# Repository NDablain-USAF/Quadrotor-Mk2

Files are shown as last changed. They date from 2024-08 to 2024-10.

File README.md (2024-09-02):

This serves as a repository for the second iteration of the autonmous quadrotor from: https://github.com/NDablain-USAF/Quadrotor
<br /> 
<br /> 
Currently in test and development
<br /> 
<br /> 
Table of Contents:<br /> 
1.0    Table of Changes<br /> 
2.0    Detailed Description of Changes         
<br /> 
<br /> 
<br /> 
1.0 Table of Changes
<br /> 
<br /> 
| Component | Was | Is |
|---:|---|---|
| Frame | Pine Wood | 3D Printed ABS |
| Motor Speed Measurement | Motor Shaft Encoders | Back EMF & ADC |
| Motor Speed Control Hardware | NPN BJT | N-Channel MOSFET |
| Motor Speed Control Software | Lead/Lag Compensator| Proportional/Integral Controller |
| Electrical Connections | Wires,Solder,Perf-Board | PCB |
| Code | C++ | C |
| MCU | Arduino Uno R3 Board | ATMega328P |
| IDE | Arduino | Microchip Studio |
| Attitude Measurement Hardware - Accelerometer | MPU 9250 Breakout Board | BMI 088 |
| Attitude Measurement Hardware - Gyroscope | MPU 9250 Breakout Board | BMI 088 |
| Attitude Measurement Hardware - Magnetometer | MPU 9250 Breakout Board | BMM 350 |
| Attitude Measurement Software | Float operations using Math.h trig. functions | Integers with polynomial trig function approximations |
| Attitude Representation | Euler Angles | Quaternions |
<br /> 
<br /> 
<br /> 
2.0 Detailed Description of Changes
<br /> 
<br /> 
  Frame: Pine wood was initially selected due to its low density, perceived ease of manipulation, and low cost. However, it was found in the Mk1 that the weight of the wood drove higher motor speed and propeller thrust requirements and it was difficult to produce multiple parts to similar dimensions by hand. The higher upfront cost of purchasing a 3D printer will allow for faster part production and replacement rates in the long term along with greater reliability in part tolerances.
  <br /> 
  <br /> 
  Motor Speed Measurement: Removing the requirement of having an integrated shaft encoder opens up a much broader range of motors to choose from, including lower priced ones. Moving from encoder counts triggered by an ISR to sampling the on board ADC allows improved control of measurement sample rate. On the ATMega328P the ADC conversion can be selected at a frequency desired by the designer, and implemented with a timer. An ISR indicates the conversion is complete, and triggers a flag for a measurement function. This greatly reduces the number of interrupts per measurement from potentially hundreds with the encoder to one with the ADC. Additionally the numbers of wires leaving the motor is reduced from five to three. 
  <br /> 
  <br /> 
  Motor Speed Control Hardware: Bipolar Junction Transistors (BJTs) require current through their base to drive current through their collector-emitter junction. This allows for a faster switching time as well as amplification as opposed to just binary saturation but requires additional components as in most cases the current supplied by an MCU IO pin is not enough to fully open the collector-emitter junction. On the other hand, a Metal Oxide Semiconductor Field Effect Transistor (MOSFET) only requires a voltage potential differenc on its gate, no current is required. This change will reduce the number of components required to control the motor speeds, decreasing cost and complexity.
  <br />
  <br />
   Motor Speed Control Software: The initial quadrotor used a lead/lag compensator to control motor speeds. This provided excellent performance, but had a higher computational complexity. First off, there were five terms to tune between the lead compensator gain, and the two poles and zeros. 4 integrals had to be taken and kept track of per motor resulting in a high RAM useage. Switching to a Proportional-Integral controller will reduce the instantaneous computation as well as the number of variables stored in RAM as only one integral will need to be maintained per motor.
   <br />
   <br />
   Electrical Connections: Hand-made connections were the primary method of attaching devices on the initial quadrotor. This allowed for rapid prototyping and the ability to easily swap damaged parts, but also drastically increased production time and quality errors. Most electrical components will be contained on a centralized PCB, several components such as the LoRa module and PA1616S GPS module will be kept on breakout boards and attached via headers to the main PCB. Hand-made connections to the motors will still have to be made with decoupling capacitors directly soldered across the motor terminals.
   <br />
   <br />
   Code: The decisions to switch from C++ to C is mainly based on the desire to learn more about the C language and perhaps reduce some of the technical baggage that can come with using C++. This means the code will take a functional approach rather than object oriented one. This will mean not using the Arduino.h libraries and instead programming primarily off of the MCU data sheet using direct register manipulation. This will allow for direct control over peripherals such as timers,counters,interrupts, and the analog to digital converter. This will likely increase development time but allow for a depper understanding of the working of the MCU.
   <br />
   <br />
Controller PCB: Screenshot (123)
  <br />
Drone PCB: Screenshot (124)
  <br />
Drone Assembly: Screenshot (125)
  <br />

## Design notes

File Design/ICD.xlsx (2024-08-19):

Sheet: CONOPS
MCU 1 will control the inner two loops to include motor speeds and attitude. It will sample the IMU and Magnetometer and be responsible for interpretting the incoming information to determine its own attitude and generate a control signal. It will generate its own motor speed references. It will receive as input a desired orientation and desired thrust, it will compensate the thrust with feedforward control based off its attitude information.

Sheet: Interface List
Component | Connects To | Via | Notes
MCU 1 | MCU 2 | SCL/PC5 | Directly
MCU 1 | MCU 2 | SDA/PC4 | Directly
MCU 1 | MCU 2 | PCINT23/PD7 | Start | PC6 | 1 | MCU 1 | 28 | PC5
MCU 1 | MCU 2 | RST/PC6 |  | PD0 | 2 |  | 27 | PC4
MCU 1 | BMM 350 | SCL/PC5 | Via logic level converter | PD1 | 3 |  | 26 | PC3
MCU 1 | BMM 350 | SDA/PC4 | Via logic level converter | PD2 | 4 |  | 25 | PC2
MCU 1 | BMM 350 | PCINT0/PB0 | Interrupt | PD3 | 5 |  | 24 | PC1
MCU 1 | BMI 088 | SCL/PC5 | Via logic level converter | PD4 | 6 |  | 23 | PC0
MCU 1 | BMI 088 | SDA/PC4 | Via logic level converter | VCC | 7 |  | 22 | GND
MCU 1 | BMI 088 | PCINT18/PD2 | Interrupt (Accel) | GND | 8 |  | 21 | AREF
MCU 1 | BMI 088 | PCINT20/PD4 | Interrupt (Gyro) | PB6 | 9 |  | 20 | AVCC
MCU 1 | Transistor 1 | OC0A/PD6 | Save 16 bit timer (Timer1) for internal timing of interrupts | PB7 | 10 |  | 19 | PB5
MCU 1 | Transistor 2 | OC0B/PD5 |  | PD5 | 11 |  | 18 | PB4
MCU 1 | Transistor 3 | OC2A/PB3 |  | PD6 | 12 |  | 17 | PB3
MCU 1 | Transistor 4 | OC2B/PD3 |  | PD7 | 13 |  | 16 | PB2
MCU 1 | Voltage Divider 1 | ADC0/PC0 | ADMUX register must be changed with right input channel prior to read, but not during a read, perhaps cycled during interrupt | PB0 | 14 |  | 15 | PB1
MCU 1 | Voltage Divider 2 | ADC1/PC1
MCU 1 | Voltage Divider 3 | ADC2/PC2
MCU 1 | Voltage Divider 4 | ADC3/PC3
MCU 1 | Header 1 | VCC | Group Header pins for easy connection to ISP
MCU 1 | Header 2 | GND
MCU 1 | Header 3 | SCK/PB5
MCU 1 | Header 4 | MISO/PB4
MCU 1 | Header 5 | MOSI/PB3
MCU 1 | Header 6 | RST/PC6
MCU 1 | Header 7 | SS/PB2
MCU 1 | Crystal Oscillator | XTAL1/PB6 | Share oscillator with MCU 2
MCU 1 | Crystal Oscillator | XTAL2/PB7
MCU 1 | Logic Level converter | OE/PB1
 |  |  |  | PC6 | 1 | MCU 2 | 28 | PC5
MCU 2 | MCU 1 | SCL/PC5 | Directly | PD0 | 2 |  | 27 | PC4
MCU 2 | MCU 1 | SDA/PC4 | Directly | PD1 | 3 |  | 26 | PC3
MCU 2 | MCU 1 | PD4 | Start | PD2 | 4 |  | 25 | PC2
MCU 2 | MCU 1 | PD7 | Reset | PD3 | 5 |  | 24 | PC1
MCU 2 | Header 1 | VCC | Group Header pins for easy connection to ISP | PD4 | 6 |  | 23 | PC0
MCU 2 | Header 2 | GND |  | VCC | 7 |  | 22 | GND
MCU 2 | Header 8 | SCK/PB5 |  | GND | 8 |  | 21 | AREF
MCU 2 | Header 9 | MISO/PB4 |  | PB6 | 9 |  | 20 | AVCC
MCU 2 | Header 10 | MOSI/PB3 |  | PB7 | 10 |  | 19 | PB5
MCU 2 | Header 11 | RST/PC6 |  | PD5 | 11 |  | 18 | PB4
MCU 2 | Header 12 | SS/PB2 |  | PD6 | 12 |  | 17 | PB3
MCU 2 | Crystal Oscillator | XTAL1/PB6 | Share oscillator with MCU 1 | PD7 | 13 |  | 16 | PB2
MCU 2 | Crystal Oscillator | XTAL2/PB7 |  | PB0 | 14 |  | 15 | PB1
MCU 2 | BMP 390 | SCK/PB5 | Via logic level converter
MCU 2 | BMP 390 | MISO/PB4 | Via logic level converter
MCU 2 | BMP 390 | MOSI/PB3 | Via logic level converter
MCU 2 | BMP 390 | CS/PB1 | Via logic level converter
MCU 2 | BMP 390 | PCINT18/PD2 | Interrupt, via logic level converter
MCU 2 | PA1616S | RXD/PD0
MCU 2 | PA1616S | TXD/PD1
MCU 2 | LoRa | SCK/PB5
MCU 2 | LoRa | MISO/PB4
MCU 2 | LoRa | MOSI/PB3
MCU 2 | LoRa | CS/PD6
MCU 2 | LoRa | GO/PB0
MCU 2 | LoRa | RST/PD5
MCU 2 | Voltage Divider | ADC0/PC0 | Track battery voltage level

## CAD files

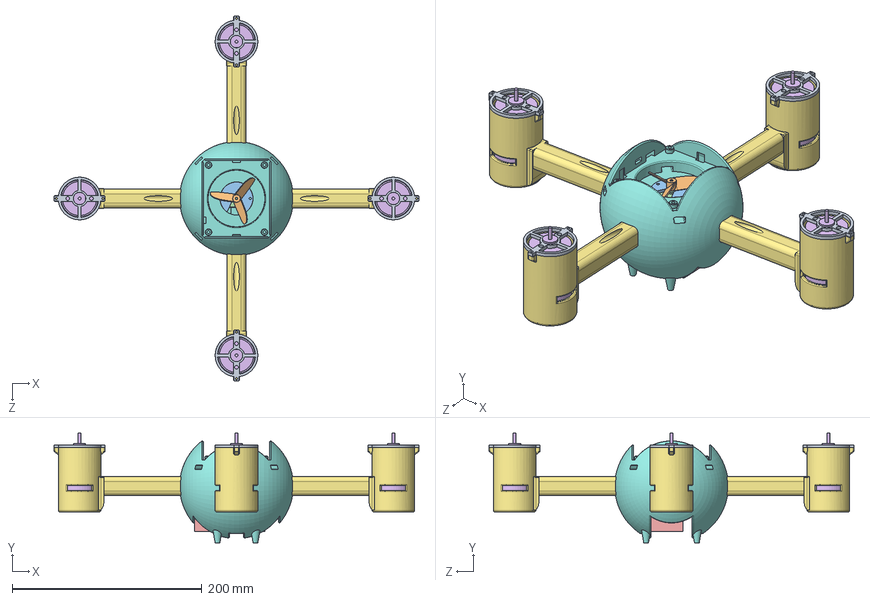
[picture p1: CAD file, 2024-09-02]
Design/Mechanical/Drone_Mark_2_v2.SLDASM
385.0 x 116.0 x 385.0 mm
Body_v2
Motor_Holder_v2 x 4
Motor x 4
Battery_3S_1500
Motor_2
Motor_2_Cover
Fan
Motor_Cover x 4

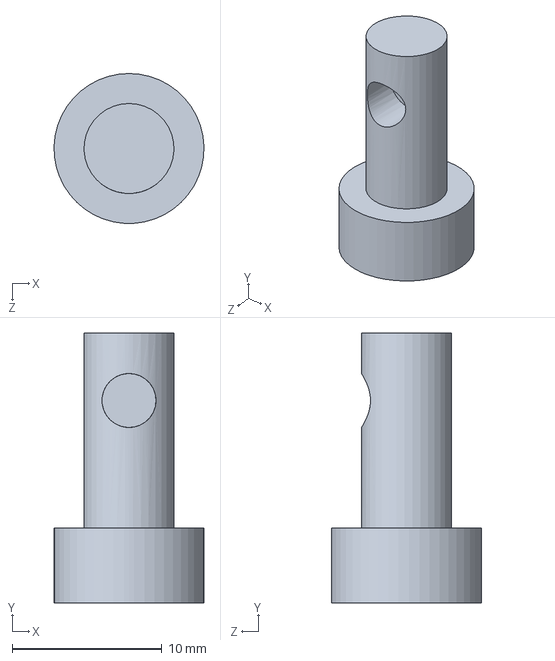
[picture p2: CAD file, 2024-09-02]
Design/Mechanical/Shaft_Extender_2.SLDPRT
9.99 x 18.0 x 10.0 mm

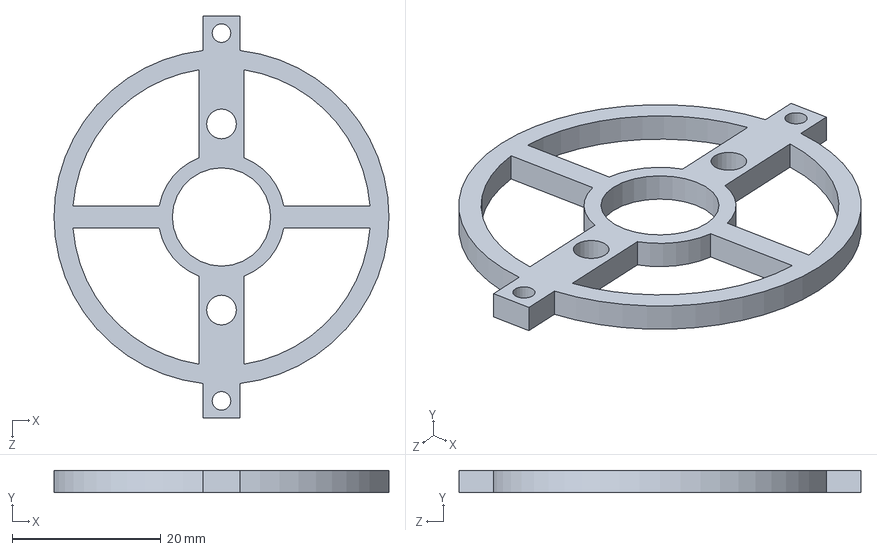
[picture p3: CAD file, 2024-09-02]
Design/Mechanical/Motor_Cover.SLDPRT
45.0 x 3.00 x 54.0 mm

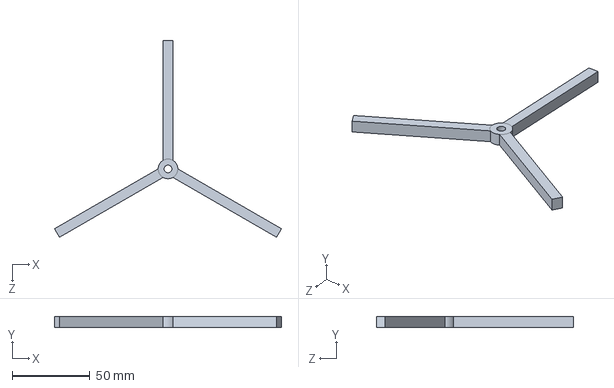
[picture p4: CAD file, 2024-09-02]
Design/Mechanical/BD6x4.2E-3-B4.SLDPRT
146.2 x 6.86 x 126.6 mm

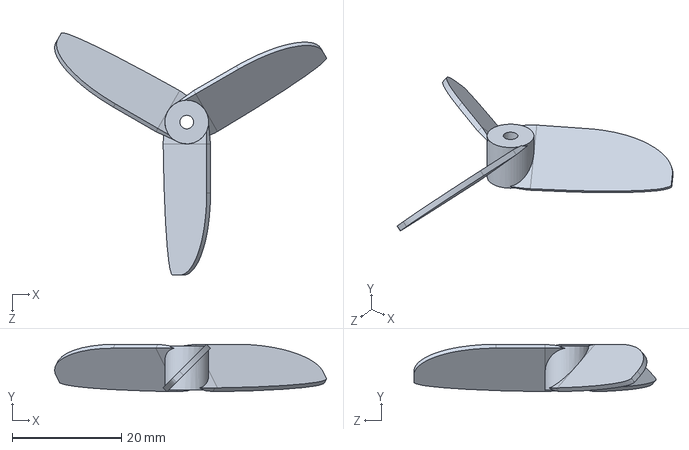
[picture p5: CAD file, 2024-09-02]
Design/Mechanical/Fan.SLDPRT
49.7 x 8.67 x 44.3 mm

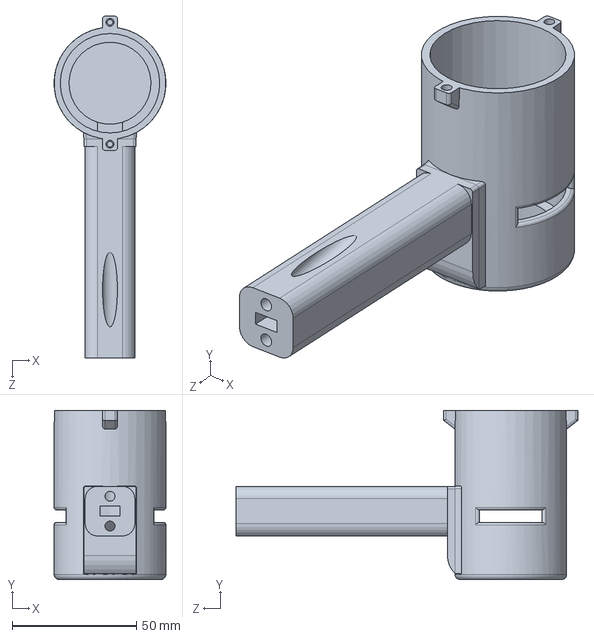
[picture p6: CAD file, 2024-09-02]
Design/Mechanical/Motor_Holder_v2.SLDPRT
45.0 x 68.0 x 137.5 mm

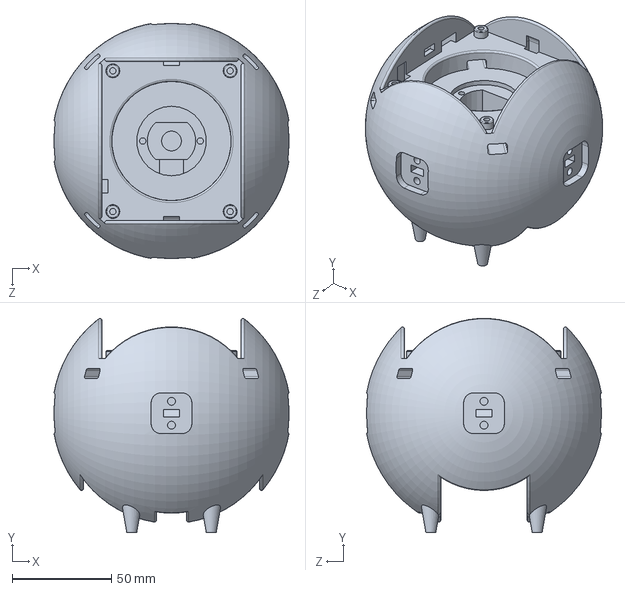
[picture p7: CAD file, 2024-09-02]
Design/Mechanical/Body_v2.SLDPRT
118.2 x 107.7 x 118.2 mm

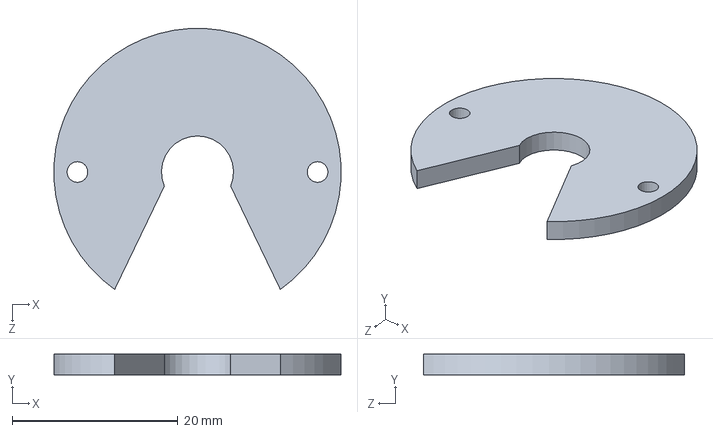
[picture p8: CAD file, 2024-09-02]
Design/Mechanical/Motor_2_Cover.SLDPRT
34.6 x 2.50 x 31.5 mm

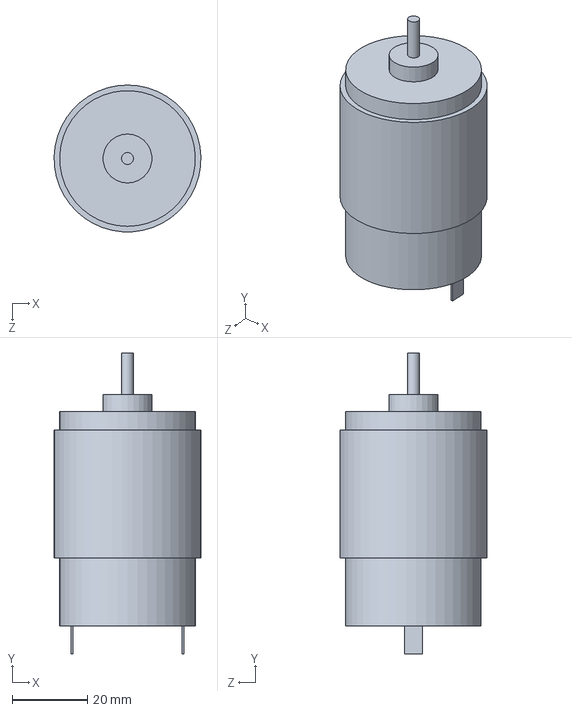
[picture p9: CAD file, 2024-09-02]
Design/Mechanical/Motor.SLDPRT
39.0 x 79.9 x 39.0 mm

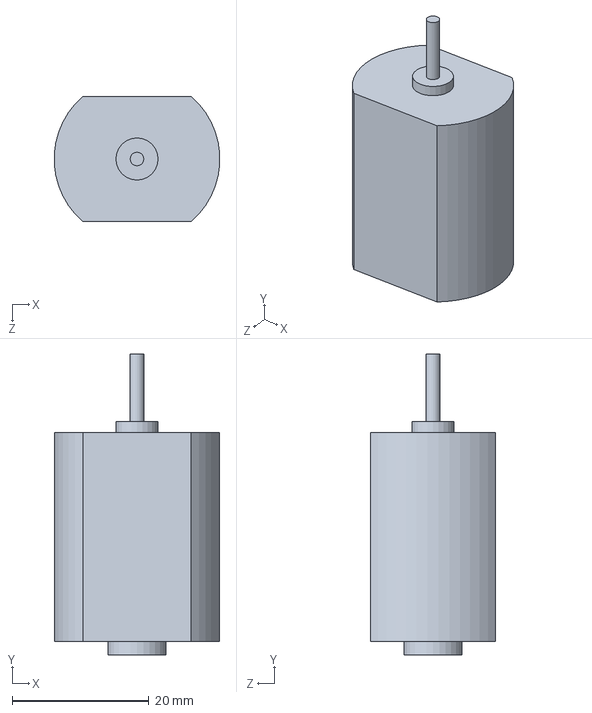
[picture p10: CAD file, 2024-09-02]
Design/Mechanical/Motor_2.SLDPRT
24.1 x 43.9 x 18.3 mm

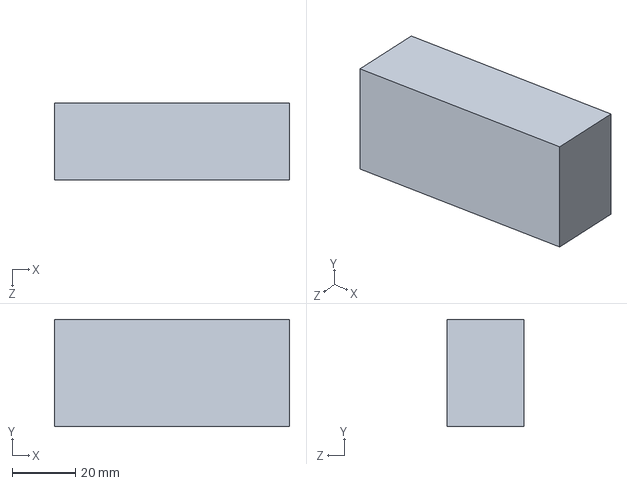
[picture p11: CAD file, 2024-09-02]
Design/Mechanical/Battery_3S_1500.SLDPRT
74.5 x 34.0 x 24.5 mm

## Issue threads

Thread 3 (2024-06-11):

Experiment with Potentiometers

NDablain-USAF, 2024-06-11:
Experiment with including potentiometers for control of motor reference speed

NDablain-USAF, 2024-06-18:
VCC-OUTPUT-GND, potentiometer is really variable voltage divider, not resistor

Closed 2024-06-18.

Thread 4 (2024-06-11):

Deep dive into I2C and Wire library

NDablain-USAF, 2024-06-11:
Read ATMega328P datasheet on I2C as well as Wire.h library implementation. Try to implement within arduino sketch first without using library.

Closed 2024-06-15.

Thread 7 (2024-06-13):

Migrate Arduino IDE sketches over to platform io

NDablain-USAF, 2024-06-13:
UnoR4 monitoring, ISP sketch, upload using ISP command

NDablain-USAF, 2024-06-21:
Not worth doing currently. Using PIO to develop and test, but Arduino IDE to flash to chip.

Closed 2024-06-21.

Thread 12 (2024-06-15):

Prototype pcb

NDablain-USAF, 2024-06-15:
Develop pcb design to include sensors and finalize list of materials needed to mount smds.

Closed 2024-06-23.

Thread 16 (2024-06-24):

Design propeller cages.

NDablain-USAF, 2024-06-24:
Add propeller cages around props to prevent damage and motor stalling in event of crash

Closed 2024-06-28.

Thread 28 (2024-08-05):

Create draft MCU1 script

NDablain-USAF, 2024-08-05:
Needs to include all the functionality MCU1 contains. ADC, I2C, Sensor Parsing, PWM Motors.

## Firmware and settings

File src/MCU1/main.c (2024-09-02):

#include "main.h"
// check number of dummy reads, for BMM350 2 are called out, perhaps only one for BMP which leads to "temp" variable? 
int main(){
	struct BMI088 IMU = {0};
	struct BMM350 MAG = {0};
	struct Motor Motor1 = {0,0,0,ref,MOTOR1_MUX};
	struct Motor Motor2 = {0,0,0,ref,MOTOR2_MUX};
	struct Motor Motor3 = {0,0,0,ref,MOTOR3_MUX};
	struct Motor Motor4 = {0,0,0,ref,MOTOR4_MUX};
	ATMega328P_Int();
	//char BMI_Status = BMI088_Int(&IMU);
	//char BMM_Status = BMM350_Int();
	while(1){
		while (g_Start_Flag==1){
			unsigned char data[3];
			unsigned char status = I2C_Read(MCU2_ADRS,1,data,2);
			unsigned int passed_variable = data[2]*256 + data[1];
			Motor1.r = passed_variable;
			//Run_BMI(BMI_Status, &IMU);
			//Run_BMM(BMM_Status, &MAG);
			Run_Motors(&Motor1,&Motor2,&Motor3,&Motor4);
		}
	}

	return 0;
}

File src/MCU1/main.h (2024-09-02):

#ifndef MAIN_H
#define MAIN_H

#ifndef F_CPU
#define F_CPU 20000000UL
#endif

#include <avr/io.h>
#include <avr/interrupt.h>
#include <util/twi.h>
#include <stdio.h>

#define MCU2_ADRS 0x10

#define ACC_ADRS 0x18 // or 0x19 if SDO1 pulled VDIO
#define ACC_DATA 0x12 // Start address of acc data, 16-bit x-y-z, LSB first
#define ACC_CONF 0x40 
#define ACC_RANGE 0x41 
#define INT2_IO_CONF 0x54 
#define INT1_INT2_MAP_DATA 0x58 
#define ACC_PWR_CTRL 0x7D
#define ACC_IIR1 0.95f
#define ACC_IIR2 0.05f

#define GYR_ADRS 0x68 // or 0x69 if SDO2 pulled VDIO
#define GYR_DATA 0x02 // Start address of gyro data, 16-bit x-y-z, LSB first
#define GYR_RANGE 0x0F 
#define GYR_BANDWIDTH 0x10
#define GYR_INT_CTRL 0x15
#define INT3_INT4_IO_MAP 0x18
#define GYR_IIR1 0.9f
#define GYR_IIR2 0.1f

#define MAG_ADRS 0x14 // or 0x15 if ADSEL pulled VDDIO
#define MAG_DATA 0x31 // Start address of mag data, 24-bit x-y-z, LSB first
#define MAG_ODR 0x04
#define MAG_MODE 0x06 
#define MAG_INT_CTRL 0x2E
#define MAG_OTP_CMD 0x50
#define MAG_XY_GAIN 0.007069978f
#define MAG_Z_GAIN 0.007174964f
#define MAG_IIR1 0.95f
#define MAG_IIR2 0.05f

#define MOTOR_CONTROL_TIME 19
#define E_INT_LIMIT 10000
#define MOTOR_C1 1009 // Motor back-EMF IIR filter coefficients
#define MOTOR_C2 15
#define MOTOR_K_P 10UL // Motor proportional control gain
#define MOTOR_K_I 4UL // Motor integral control gain
#define MOTOR_K_D 128UL // Motor derivative control gain
#define ref 150
#define MOTOR1_MUX (1<<REFS0)
#define MOTOR2_MUX ((1<<REFS0) | (1<<MUX0))
#define MOTOR3_MUX ((1<<REFS0) | (1<<MUX1))
#define MOTOR4_MUX ((1<<REFS0) | (1<<MUX0) | (1<<MUX1))

volatile char g_Start_Flag = 0;
volatile char g_Acc_Flag = 0;
volatile char g_Gyr_Flag = 0;
volatile char g_Mag_Flag = 0;
volatile char g_Motor_Flag = 0;
volatile char g_ADC_Flag = 0;

struct BMI088 {
    float Accel_X;
    float Accel_Y;
    float Accel_Z;
    float W_X;
    float W_Y;
    float W_Z;
    float W_X_bias;
    float W_Y_bias;
    float W_Z_bias;
};

struct BMM350 {
	float Mag_X;
	float Mag_Y;
	float Mag_Z;
};

struct Motor {
	int e_int;
	unsigned long x;
	int e_last;
	unsigned int r;
	unsigned char mux;
};

void Detain(unsigned long length){
	// A reproduction of the delay() function, prevents overwhelming the serial monitor
	for (unsigned long i=0;i<length;i++){asm("");}
}

void SPI_Int(){
	DDRB |= (1<<PINB5) | (1<<PINB3) | (1<<PINB2); // Set SCK, MOSI, and SS as outputs
	PORTB |= (1<<PINB2); // Set SS high
	SPCR |= (1<<SPE) | (1<<MSTR) | (1<<SPR0); // Enables SPI, sets AVR as master, sets clock to f_osc/16
}

void SPI_Transmit_Char_Data_Visualizer(unsigned char* outbound, unsigned char length){
	PORTB &= ~(1<<PINB2); // Set B2 LOW
	unsigned char i = 0;
	while (i++<length){
		SPDR = *outbound++; // Put data into data register
		while (!(SPSR & (1<<SPIF))){asm("");} // Wait for flag to be set in status register to continue
	}
	SPDR = 10; // Line feed
	while (!(SPSR & (1<<SPIF))){asm("");}
	PORTB |= (1<<PINB2); // Set B2 HIGH
}

void SPI_Transmit_Long_Data_Visualizer(long outbound, unsigned char length, unsigned char option){
	char buffer[length];
	unsigned char n = snprintf(buffer,length,"%ld",outbound);
	PORTB &= ~(1<<PINB2); // Set B2 LOW
	for (unsigned char i=0;i<n;i++){
		SPDR = buffer[i]; // Put data into data register
		while (!(SPSR & (1<<SPIF))){asm("");} // Wait for flag to be set in status register to continue
	}
	if (option==2){SPDR = 10;} // Line feed
	else {SPDR = 44;} // ,
	while (!(SPSR & (1<<SPIF))){asm("");}
	PORTB |= (1<<PINB2); // Set B2 HIGH
}

unsigned char SPI_Write_Register(char Port, char Pin, char Register, unsigned char Data){
	if (Port==1){PORTB &= ~(1<<Pin);}
	else if (Port==2){PORTC &= ~(1<<Pin);}
	else if (Port==3){PORTD &= ~(1<<Pin);}

	SPDR = (Register|(1<<7)); // Send register to write to, 7th bit must be 1 for write
	while (!(SPSR & (1<<SPIF))){asm("");} // Wait for flag to be set in status register to continue
	SPDR = Data; // Send new value
	while (!(SPSR & (1<<SPIF))){asm("");}
	unsigned char inbound = SPDR;
	
	if (Port==1){PORTB |= (1<<Pin);}
	else if (Port==2){PORTC |= (1<<Pin);}
	else if (Port==3){PORTD |= (1<<Pin);}
	
	return inbound;
}

void SPI_Read_Register(char Port, char Pin, char Register, unsigned char* buffer, unsigned char length){
	if (Port==1){PORTB &= ~(1<<Pin);}
	else if (Port==3){PORTD &= ~(1<<Pin);}
	else if (Port==2){PORTC &= ~(1<<Pin);}

	SPDR = Register; // Send register to read from, 0 in 7th bit signifies read command
	while (!(SPSR & (1<<SPIF))){asm("");} // Wait for flag to be set in status register to continue
	unsigned char i = 0;
	while(i++<length){
		SPDR = 1; // Must perform a dummy write even during read
		while (!(SPSR & (1<<SPIF))){asm("");} // Wait for flag to be set in status register to continue
		*buffer = SPDR;
		++buffer;
	}
	
	if (Port==1){PORTB |= (1<<Pin);}
	else if (Port==3){PORTD |= (1<<Pin);}
	else if (Port==2){PORTC |= (1<<Pin);}
}
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

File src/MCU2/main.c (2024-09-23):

#include "main.h"

int main(void){
	ATMega328P_Init();
	SPI_Init();
	//I2C_Init();
	LoRa_Init();
	struct BMP barometer = {0};
	BMP_Init(&barometer);
	int passed_variable = 0;
    while(1){
		LoRa_Read(&passed_variable);
        BMP_Read(&barometer);
		//unsigned char data[2] = {0,0};
		//data[0] = (unsigned char)passed_variable;
		//data[1] = passed_variable>>8;
		//unsigned char status = I2C_Slave_Transmit(data,2);
		SPI_Transmit_Long_Data_Visualizer((long)passed_variable,10);
        SPI_Transmit_Float_Data_Visualizer(barometer.height,10);
		Detain(10000UL);
    }
	return 0;
}

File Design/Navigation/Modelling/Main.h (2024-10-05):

#ifndef MAIN_H
#define MAIN_H

#define I_XX_EST 0.013787f
#define I_XX_REAL 0.015f
#define I_YY_EST 0.013795f
#define I_YY_REAL 0.013f
#define I_ZZ_EST 0.026414f // kg-m^2
#define I_ZZ_REAL 0.028f
#define M_EST 1.409f // Estimated mass of drone in kg
#define M_REAL 1.50f // Real mass of drone in kg
#define L_EST 0.1555f // Distance from center of drone to propeller
#define L_REAL 0.16f
#define G_EST 9.81f // Acceleration due to gravity m/s^2
#define G_REAL 9.79f
#define D_T 0.001f // Integration time
#define T_F 30.0f // Final time of simulation
#define K_F 0.000003125f // Relates thrust (N) to motor speed in (rad/s)^2
#define K_T 0.000000037f // Relates torque (N-m) to motor speed in (rad/s)^2 

#define PI 3.1415f
#define D2R (PI/180.0)

double Reference[4] = {5.0,0.0,0.0,0.0}; // Height, Roll, Pitch, Yaw
const double K_Roll[3] = {4.6749,3.2607,1.0440};
const double K_Pitch[3] = {4.6750,3.2607,1.0440};
const double K_Yaw[3] = {4.7325,3.3183,1.0841};
const double K_Thrust[4] = {0.3,0.03,1.1,0.001};

struct Motor {
    double e;
    double e_int;
    double Speed;
};

struct Quadrotor{
    double Displacement[3]; // Inertial Position, x-y-z, m
    double Euler[3]; // Euler angles, roll-pitch-yaw, rad
    double Angular_Rate[3]; // Body Angular Rate, x-y-z, rad/s
    double Velocity[3]; // Body velocity, x-y-z, m/s
    double Force_Output[3];
    double Moment_Output[3];
    double Thrust_Requested;
    double Moment_Requested[3];
    struct Motor Motor1; // Front
    struct Motor Motor2; // Right 
    struct Motor Motor3; // Rear
    struct Motor Motor4; // Left
};

double Low_Pass_Filter(double Speed_Ref, double Speed_Current){
    // Motor is modeled as a low pass filter, 20/(s+20) = O_p/I_p -> O_p*(s+20) = 20*I_p...
    // O_p*s = 20*(I_p-O_p);
    double Motor_Accel = 20.0*(Speed_Ref-Speed_Current);
    return ((Motor_Accel*D_T) + Speed_Current);
}

void Control(struct Quadrotor* Drone){
    double D_T2 = 0.01;
    static double e_int[4];
    static double e_int2 = 0;
    double e[4];
    static double e_last = 0;
    // Thrust, uses PID feedback combined with feedforward control to counter gravity
    e[0] = Reference[0]-Drone->Displacement[2];
    e_int[0] += (e[0]*D_T2);
    e_int2 += (e_int[0]*D_T2);
    double Feed_Forward = M_EST*G_EST*(1/cos(Drone->Euler[0]))*(1/cos(Drone->Euler[1]));
    double Feed_Back = (K_Thrust[0]*e[0]) + (K_Thrust[1]*e_int[0]) + K_Thrust[2]*((e[0]-e_last)/D_T2) + (K_Thrust[3]*e_int2);
    Drone->Thrust_Requested = Feed_Forward + Feed_Back;
    e_last = e[0];
    // Torques, uses tracking LQR
    for (int i=1;i<4;i++){
        e[i] = Reference[i]-Drone->Euler[i-1];
        e_int[i] += (e[i]*D_T2);
    }
    Drone->Moment_Requested[0] = K_Roll[0]*e_int[1] - K_Roll[1]*Drone->Euler[0] - K_Roll[2]*Drone->Angular_Rate[0];
    Drone->Moment_Requested[1] = K_Pitch[0]*e_int[2] - K_Pitch[1]*Drone->Euler[1] - K_Pitch[2]*Drone->Angular_Rate[1];
    Drone->Moment_Requested[2] = K_Yaw[0]*e_int[3] - K_Yaw[1]*Drone->Euler[2] - K_Yaw[2]*Drone->Angular_Rate[2];
}
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

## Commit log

2024-06-13 MCU, IMU, Magnetometer Datasheets
2024-06-13 MCU, IMU, and Magnetometer Datasheets
2024-06-14 Create I2C
2024-06-14 Update and rename I2C to I2C.cpp
2024-06-27 Proof of concept of Quaternion navigation
    This iteration shows the ability of a Kalman filter using only the gravity vector (no magnetometer) to correctly predict the quaternion describing a rotating body in the presence of noise.
2024-06-27 Practice PCB
    First PCB design to show proof of concept of soldering SMDs and integrating MCU with sensors directly.
2024-07-02 IMU using Quaternions
2024-08-02 Update SPI.c
    Test sprintf and sending longer numbers
2024-08-02 Update and rename src/Examples/SPI.c to src/Examples/SPI/SPI.c
2024-08-05 Update and rename I2C.cpp to I2C.C
2024-09-02 Update and rename main.c to UART.c
